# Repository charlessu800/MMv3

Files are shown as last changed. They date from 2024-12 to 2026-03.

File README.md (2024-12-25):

# MMv3

MMv3 is the 3rd generation robot platform used to teach the IEEE Micromouse DeCal at UC Berkeley. It was designed with usability, manufacturability, size, and cost in mind.

## Schedule

Skeleton lab code, lab documents, and solutions are stored in [labs/](labs/), [docs/](docs/), and [solutions/](solutions/), respectively. To get started with a lab, simply copy the contents of the folder over to the CircuitPython drive and edit files from there.

* [lab1](docs/lab1.md) - CircuitPython Basics
* [lab2](docs/lab2.md) - Assembly
* [sanity](docs/sanity.md) - Hardware Check
* [lab3](docs/lab3.md) - Encoders
* [lab4](docs/lab4.md) - IR Sensors
* [lab5](docs/lab5.md) - Odometry and Motor Control
* **Checkpoint 1**: Does your mouse drive?
* [lab6](docs/lab6.md) - Intro to PID
* [lab7](docs/lab7.md) - More PID
* **Checkpoint 2**: Does your mouse straight under PID control?
* [lab8](docs/lab8.md) - Maze Solving Primitives **(WIP)**

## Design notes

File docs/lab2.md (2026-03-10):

# Lab 2: Assembly

## Quick Check

First thing you should do before you move on with the rest of the lab is to plug your Pi Pico into your computer and make sure it shows up in your file system like so: 

(NOTE: the image below shows a drive named CIRCUITPY but you probably will see a drive named RPI-RP2. This is expected)
<p align="center">
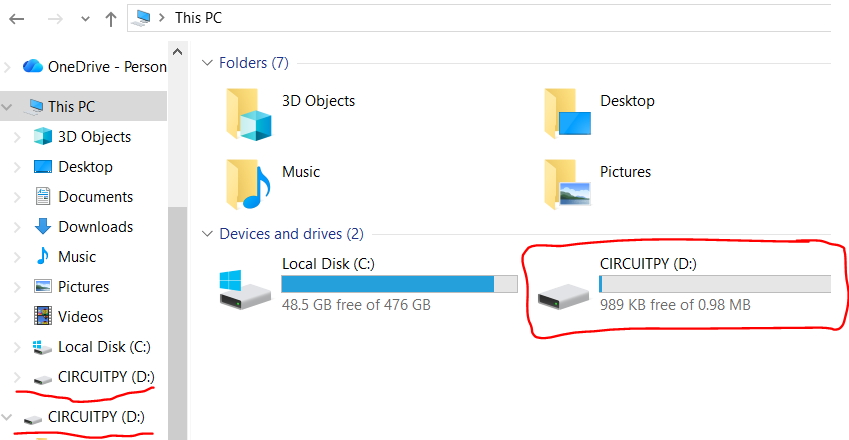
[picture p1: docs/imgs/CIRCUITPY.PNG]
    
    <br>
    <a><b>Updated CIRCUITPY Drive Directory Example image in Windows 10 File Explorer</b></a>
</p>
If the Pi Pico when connected to your PC does not show up like the image above shows try a different cable. If that does not work, try a different PC. Finally, if all the above does not work ask your TA for help.

## Assembly

Download [`ibom.html`](https://github.com/charlessu800/MMv3/releases/download/MMv3.5/ibom.html) and open it in your preferred browser. The interactive BOM (bill of materials) shows what parts are needed on your mouse's PCB (printed circuit board) and where they need to be placed. This html file will be very helpful when assembling your mouse.

To see images of all the individual parts, see the Google Drive link [here](https://drive.google.com/drive/folders/1rGae82BSrE_mvmMwKTBHT9P-unDKIKQj?usp=sharing).

### Reflow Soldering

Let's start with the back of the PCB which is where the majority of parts are located. In the `ibom.html` file you have downloaded then opened in your a browser, click `B` in the top right (highlighted in red) to show just the back side of the PCB. Make sure it looks like below.

<p align="center">
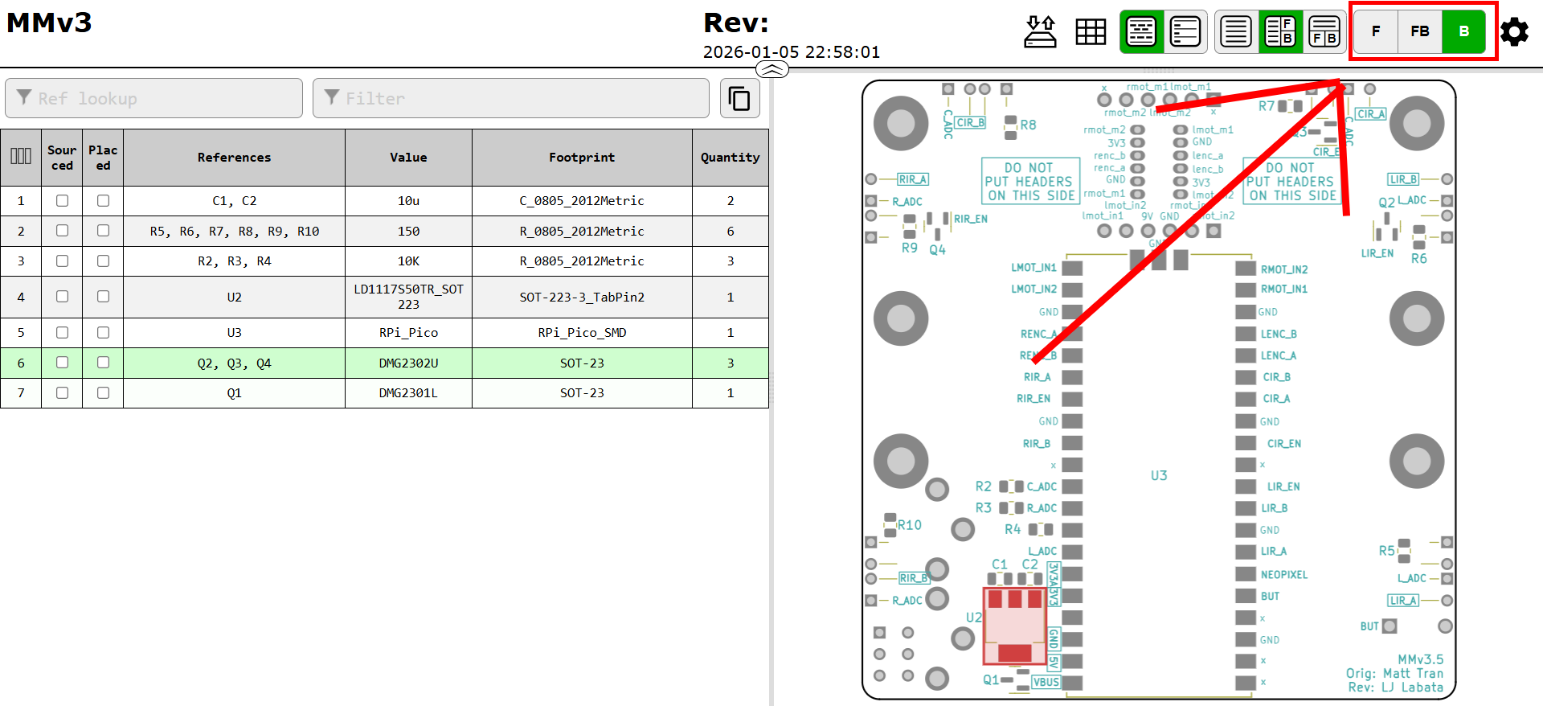
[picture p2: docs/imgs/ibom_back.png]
    
    <br>
    <a><b>iBOM Back</b></a>
</p>

Rather than solder each part by hand, we'll use reflow soldering which does it all at once. In reflow soldering, we place components on top of pads covered in solder paste before sending the whole thing through an oven to melt the solder, making permanent joints.

<p align="center">
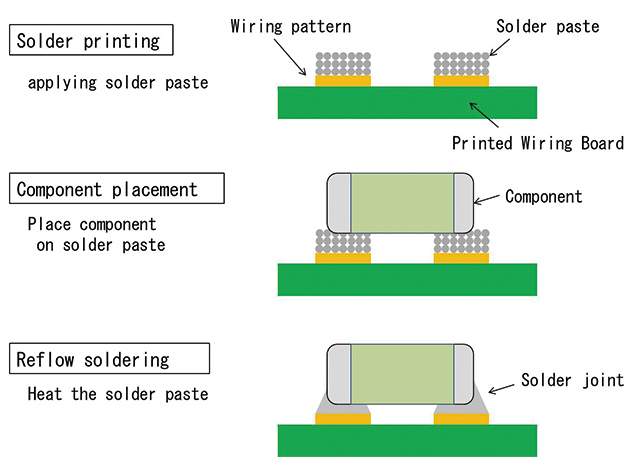
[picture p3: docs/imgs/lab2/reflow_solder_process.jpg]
    
    <br>
    <a><b>Reflow Solder Process</b></a>
</p>

Let's start by applying the solder paste using a **solder stencil**. Instead of squeezing the perfect amount onto each pad by hand, we can do it all at once by spreading paste over a stencil with holes cut out precisely where we want paste. For a good solder paste application, it's important to make sure the stencil is flush against the PCB and stays aligned. Tape the stencil onto the table to keep the stencil from moving. The process is very forgiving, so don't worry if your paste looks messy or goes a bit outside the pads after having applied the paste with the stencil. You can use tweezers or something like it to clean up places where pads are shorted togehter. Please ask the TAs if you have any questions about this.  

<p align="center">
    
    
    
    <br>
    <a><b>Solder Paste Application Process</b></a>
</p>

Now it's time for component placement. Following the `ibom.html`, place all of the components for the back side. None of the symmetric components have polarity, so don't worry about part orientation. Tweezers will be very useful, but don't squeeze too hard or your component will go flying. Again, the process is quite forgiving so don't worry if your parts aren't perfectly aligned as solder surface tension will generally pull them into alignment.

<p align="center">
    
    
    
    <br>
    <a><b>Component Placement</b></a>
</p>

> [!IMPORTANT]  
> Before moving on, double check that you correctly placed each component in the right place and the right orientation.
> - Are your MOSFET transistors in the right place? Remember that there are 3 x n-channel MOSFETs (Q2,Q3,Q4) and **1 x p-channel MOSFET (Q1)**.
> Now you are ready to show one of your TAs to give it one last lookover before getting reflowed.

Finally, let's reflow the solder! Bring you board with the placed components to your TA. They will do a final check before throwing your board into the reflow oven, loading up the correct profile, and waiting. With any luck, all of your joints will melt and the back side of your board will be done.

<p align="center">
    
    
    <br>
    <a><b>Reflow</b></a>
</p>

### Hand Soldering

The rest of the components need to be attached by hand. The general process is to heat up both the pad and the part before melting solder onto both of them. Adafruit has a great list of common issues and fixes which can be found [here](https://learn.adafruit.com/adafruit-guide-excellent-soldering/common-problems).  

<p align="center">
    
    <br>
    <a><b>How to Make a Solder Joint</b></a>
</p>

Let's start off with the mouse's main PCB. Click `F`, located in the top right of the `ibom.html`, to see the remaining components.

<p align="center">
    
    <br>
    <a><b>iBOM Front</b></a>
</p>

You can hand solder all the components on the Front side of the PCB in any order but there is a preferred way to do so that will be less of a headache when soldering.
1. D2 - D13 (THT LEDs)
2. SW1, SW2 (THT Switches)
3. DRV8833 (Motor Drive Module)
4. J3, J4 (ZH Series JST 6-pin connector)
5. J2, J5 (Receptacle Connector 0.100" (2.54mm) Through Hole Gold)
6. J1 (Keystone_593_594 Battery Contact Snaps)

This is also the order in how the lab has been laid out.

First we solder the IR LEDs. Note that the silkscreen should denote the polarity. The longer line corresponds to the longer leg of the IR LEDs. They also need to be mounted at a right angle so don't be afraid to bend them. Splaying the leads outward should hold them in place while you apply solder. After you solder them you can cut off the excess legs of the IR LEDs but be careful! The ends will fly off when cutting so protect your eyes. Look away if you don't have glasses ;(

<p align="center">
    
    
    <br>
    <a><b>IR LEDs</b></a>
</p>

Next, solder the SW1, SW2 (THT Switches). These components do now have polarity so their orientation does not matter. Additionally, you should solder these switches such that they are on the Front side of the board but if you do not that is okay. They still will work.
<p align="center">
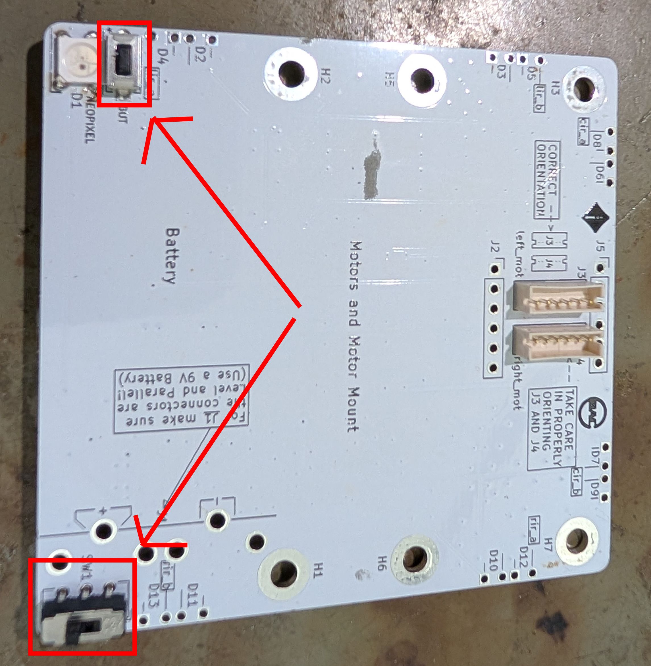
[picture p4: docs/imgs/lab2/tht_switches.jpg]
    
    <br>
    <a><b>THT Switches</b></a>
</p>

Now, the DRV8833 motor driver board. Solder the two 6-pin headers onto the board and bridge the `en` pads as shown in the following pictures. Make sure when soldering the two 6-pin headers that you are placing them on the correct side of the board. It should look like the final image below where the `en` pads are on top.

The technique that I find works best is to solder just one pin first with the part in any orientation. Then reheat that joint while pressing on the part to move it into perfect alignment. Finally, do the rest of the pins.

<p align="center">
    
    
    
    
    <br>
    <a><b>DRV8833 Motor Driver Assembly</b></a>
</p>

Finally, let's add the connector components! We saved these for last because if we did them any sooner it would make soldering the rest of the board more awkward. This is because the bigger components, like the battery connectors and motor connectors, would make it almost impossible to lay the pcb flat on a table.

> [!NOTE]
> Be sure that when you solder these bigger components, motor connectors and such, you place them on the correct side of the board, the Front side. That side is the side opposite of the pi pico. DO NOT solder these bigger components on the same side as the green pi pico. You will save yourself a lot of headaches :D

Lets start by soldering first the J3, J4 (ZH Series JST 6-pin connector) components

<p align="center">
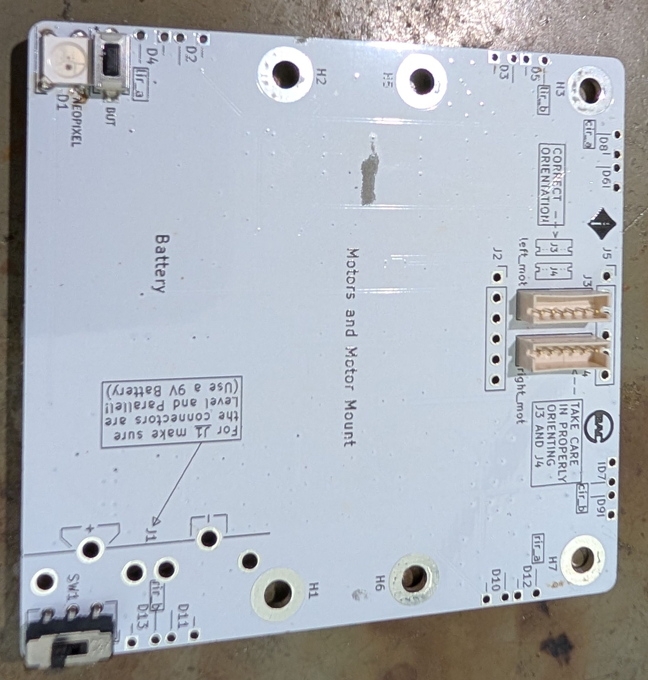
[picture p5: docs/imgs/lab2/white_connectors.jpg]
    
    <br>
    <a><b>J3, J4 (ZH Series JST 6-pin connector)</b></a>
</p>

Next solder first the J2, J5 (Receptacle Connector 0.100" (2.54mm) Through Hole Gold)

<p align="center">
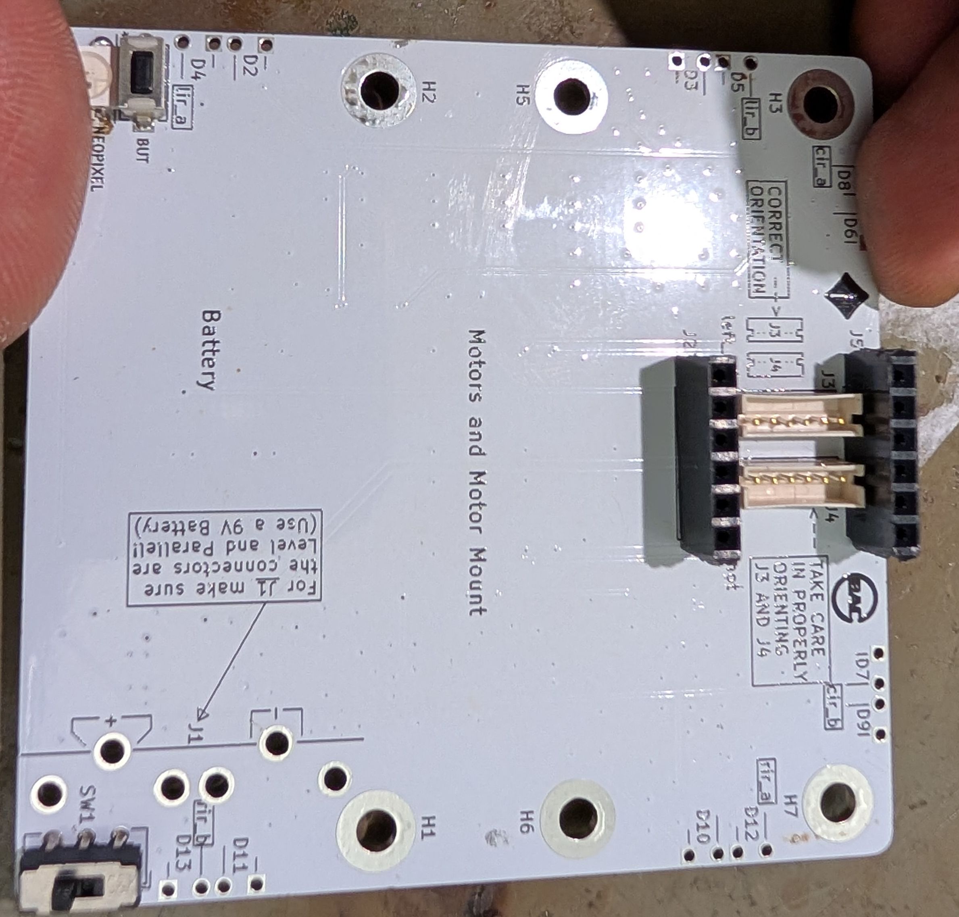
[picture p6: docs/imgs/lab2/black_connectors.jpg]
    
    <br>
    <a><b>J2, J5 (Receptacle Connector 0.100" (2.54mm) Through Hole Gold)
</b></a>
</p>

Now let's solder the J1 (Keystone_593_594 Battery Contact Snaps) connectors. When soldering these connectors it is advised to take the two Battery Contact Snaps, positive and negative, and attach them to a 9V battery first before placing them on the board. See the images below. This is to make sure that when you solder them onto the board they are aligned. You can solder the Battery Contact Snaps while the 9V battery is still connected to them. (In these photos the directionality of the motor contorller unit is facing the wrong way, the point where you bridge the pads should be closer to the left side.) 

<p align="center">
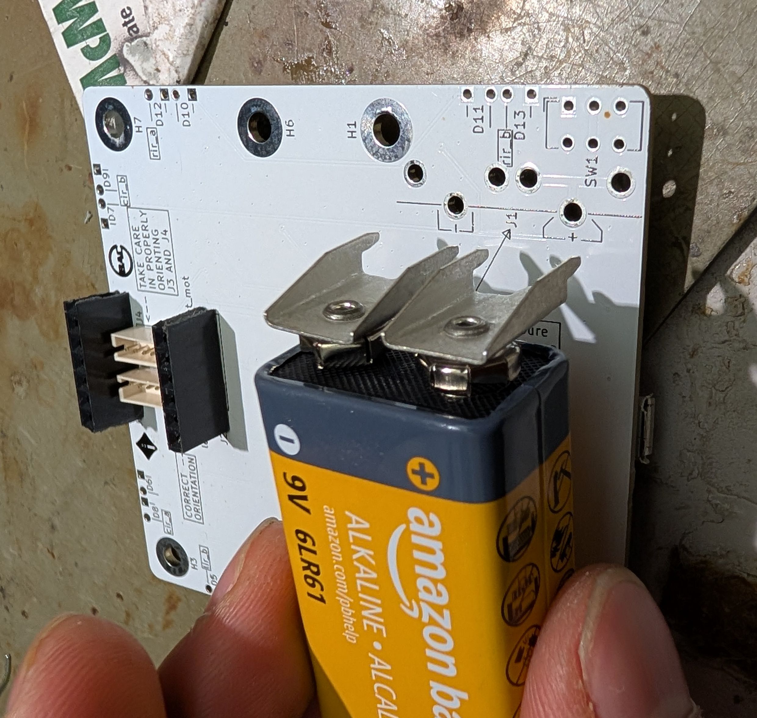
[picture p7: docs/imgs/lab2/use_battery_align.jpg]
    
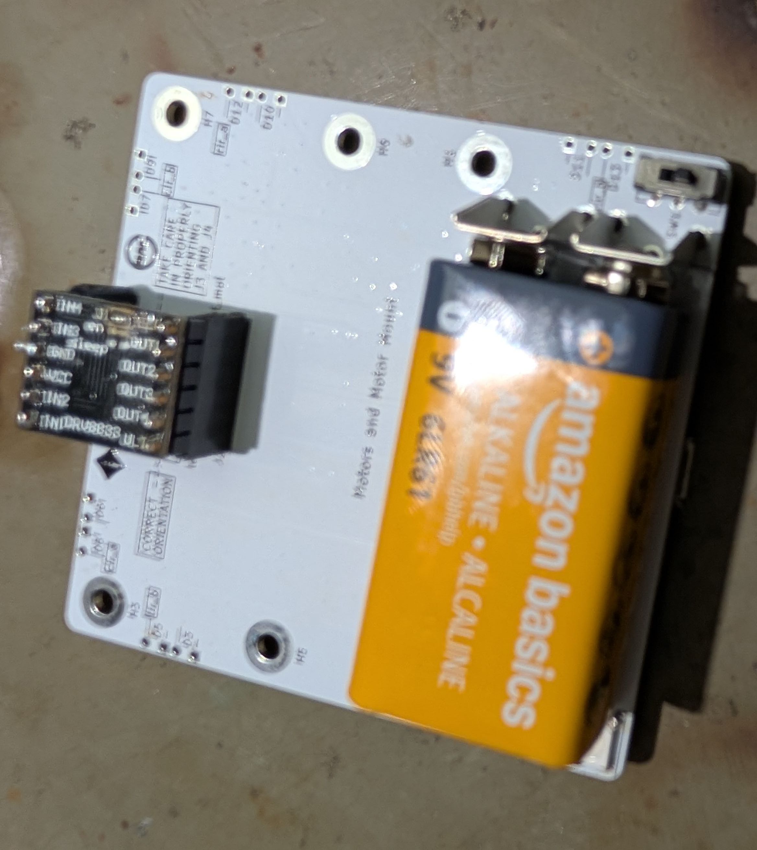
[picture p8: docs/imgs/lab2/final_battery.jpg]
    
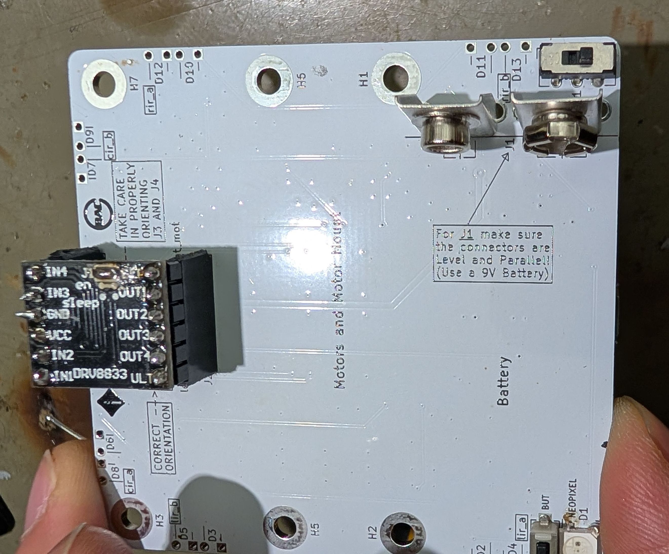
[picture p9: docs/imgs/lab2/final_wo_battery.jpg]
    
    <br>
    <a><b>Using a 9V Battery for Alignment of the J1 (Keystone_593_594 Battery Contact Snaps)
</b></a>
</p>

Additionally, make sure that you place the two Battery Contact Snaps in each of their respectative places. 

<p align="center">
    
    <br>
    <a><b>Good Placement
</b></a>
</p>

<p align="center">
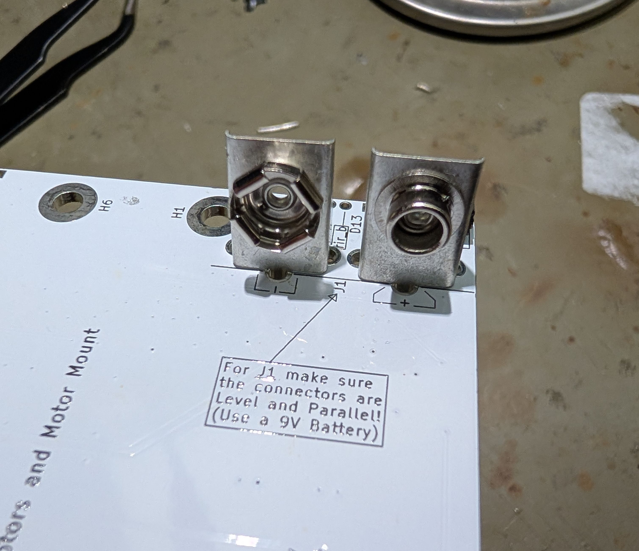
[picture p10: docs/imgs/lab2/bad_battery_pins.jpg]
    
    <br>
    <a><b>Bad Placement
</b></a>
</p>

With any luck, your board should be finished! At least all the soldering :)

<p align="center">
    
    <br>
    <a><b>PCB with completed soldered components</b></a>
</p>

### Optional SMD LED Component

We made the D1 Neopixel LED component optional as it's one of the hardest parts to solder. It is the only hand soldered SMD component. The Neopixel LED uses the same soldering process except there's no hole to stick the part through. Please see this [video (skip to 2:16)](https://youtu.be/RODp8HSlFPA?t=136) on soldering such components if you want to give this a try. You will need tweezers.

<p align="center">
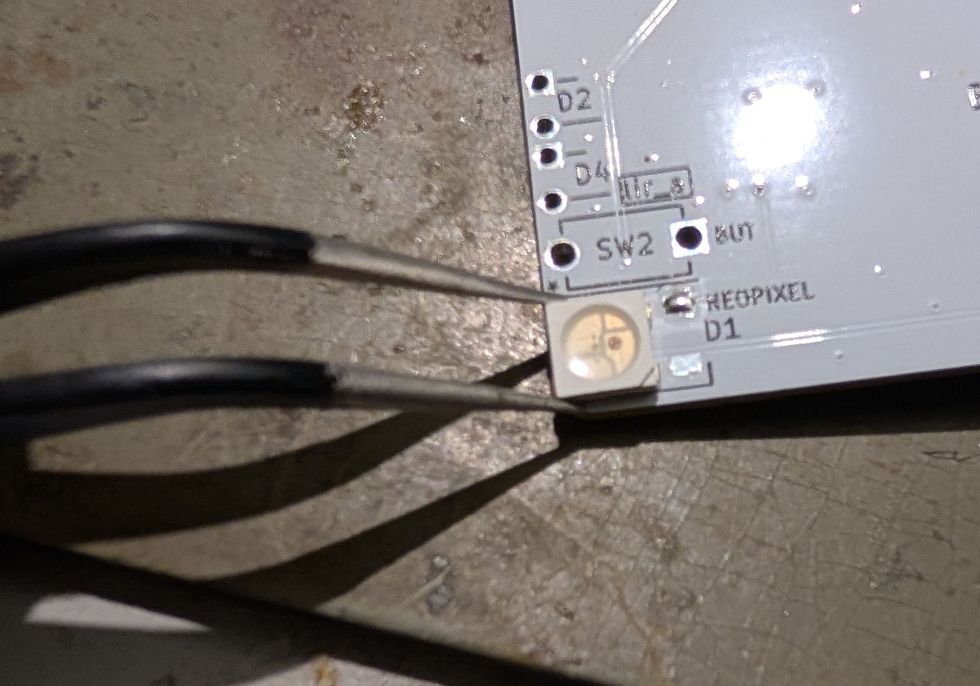
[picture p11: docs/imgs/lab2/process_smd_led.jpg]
    
    <br>
    <a><b>Part of the process to solder D1 Neopixel LED with tweezers</b></a>
</p>

> [!NOTE]  
> The Neopixel has a polarity or in other words a specific orientation that it must be placed in when soldering. You must place this part correctly in order for this Neopixel LED to work. Align this triangular indent on the Neopixel as shown below when soldering, highlighted in red. 

<p align="center">
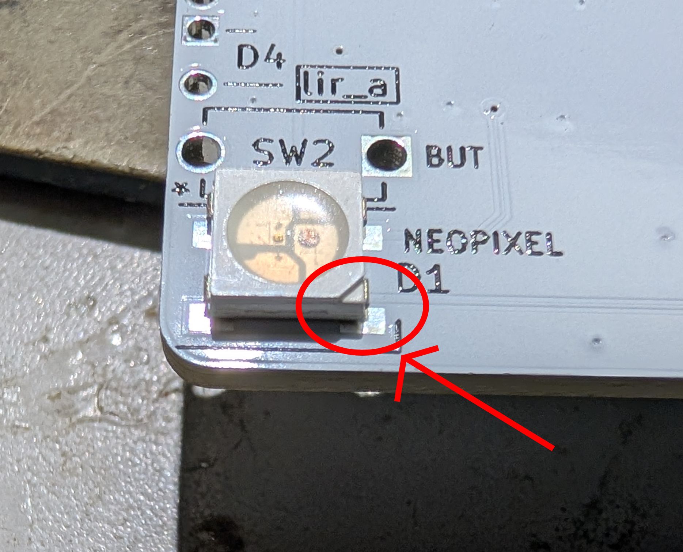
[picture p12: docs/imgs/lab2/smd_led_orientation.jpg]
    
    <br>
    <a><b>SMD LED Proper Orientation</b></a>
</p>

### Partial Mechanical Assembly

We will only partially assembly the mechanical parts of the mouse first before assembling it all in one go. We do this to make swapping out motors easier if one motor does not work (hopefully not the case). So just connect the put the motors into their 3D printed motor housing and connect them to the board using the cables for now. Then check if the motors work by running the sanity check that we talk more about below.

<p align="center">
    
    
    <br>
    <a><b>Partial Assembly</b></a>
</p>

> [!IMPORTANT]  
> Make sure that when you plug in the motor cables that they are plugged in all the way. Below are what a good motor cable plugged connection looks like and a bad one. Do this before running the sanity check code.

<p align="center">
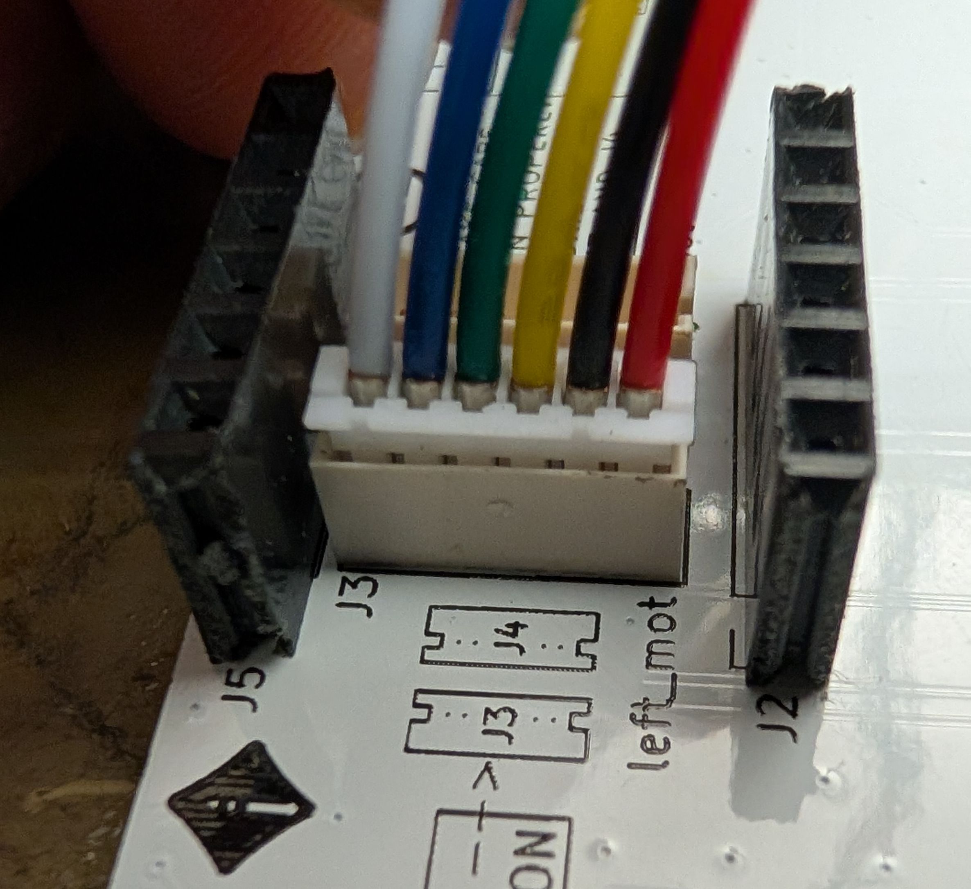
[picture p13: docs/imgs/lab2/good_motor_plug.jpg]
    
    <br>
    <a><b>Good - Motor Cables plugged in all the way</b></a>
</p>

<p align="center">
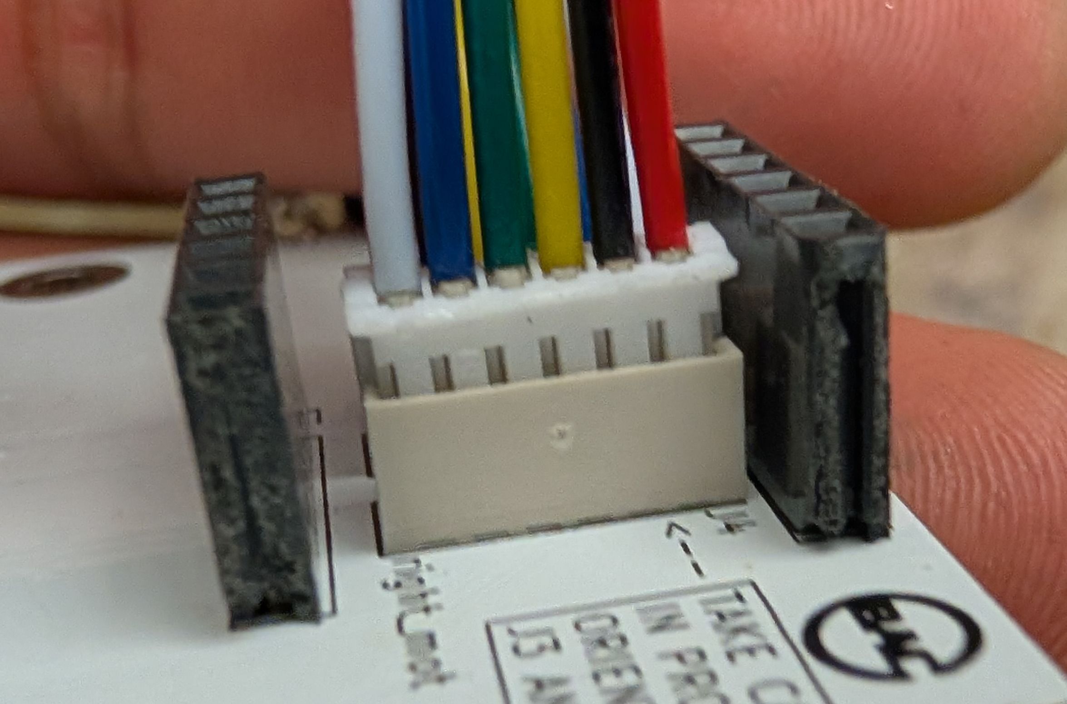
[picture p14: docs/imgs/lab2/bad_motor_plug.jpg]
    
    <br>
    <a><b>Bad - Motor Cables not plugged in all the way</b></a>
</p>

## Sanity Check

Now before we fully assembly your mouse we will make sure everything is working by running a [sanity check](sanity.md).
That means check to see that each of the 6 pairs of IR LEDs work, that each of the two motors spin as they should, and that the encoders work by outputting data that makes sense. You can find out more of what this means by following the [sanity check](sanity.md) document. 

## IR Calibration

If you placed your mouse against a reflective surface, you may have noticed that the IR readings change. Since our sensors are currently mounted perpendicular to the mouse, they pick up some reflection from the surface the mouse sits on. To fix this, we're going to bend our IR sensors ever so slightly upwards to compensate.

Bring up the sanity check again to the IR sensor printout section. Bend your IR sensors upwards just enough so that the difference between pointing them into free space and placing them on a surface is less than 2,000.

<p align="center">
    
    <br>
    <a><b>Bent IR Sensors</b></a>
</p>

### Final Mechanical Assembly

Yay you made it! Let's finish assembling the mouse. Follow the pictures below. The screw threads are printed into the plastic so don't overtighten them. Don't be afraid to apply a bit of force when attaching the wheels since a tighter fit improves concentricity.

<p align="center">
    
    
    
    
    
    <br>
    <a><b>Final Assembly</b></a>
</p>

### Checkoff #1

1. Show your mentor your assembled mouse, passing sanity check, and calibrated IR sensors.

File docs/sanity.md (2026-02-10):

# Sanity

This lab provides the instructions and code to test all aspects of your mouse and identify any hardware defects. If at any point in this lab a test is not passed, refer to this document to [troubleshoot](troubleshooting.md) your mouse. If, after trying to troubleshoot your mouse on your own with the aforementioned document, it is still not working, ask an instructor for further help debugging.

1. Upload the firmware onto your Raspberry Pi Pico

Plug the mouse, aka the Pi Pico, into your computer and upload the latest **firmware.uf2** (see [releases](https://adafruit-circuit-python.s3.amazonaws.com/bin/raspberry_pi_pico/en_US/adafruit-circuitpython-raspberry_pi_pico-en_US-8.2.0.uf2) by dragging the file into the `RPI-RP2` folder that shows up. The RPI-RP2 folder is shown in the following image.

[TODO: ADD RPI-RP2 Drive Directory Example image]
*RPI-RP2 Drive Directory Example image*

It should disappear and reappear as a `CIRCUITPY` folder. As the following image shows.
<p align="center">
    
    <br>
    <a><b>Updated CIRCUITPY Drive Directory Example image in Windows 10 File Explorer</b></a>
</p>

> [!NOTE]  
> If you've uploaded firmware before onto the Pi Pico, you'll need to hold the `BOOTSEL` button on the Pi Pico while plugging in. In more detail, first make sure to unplug the Pi Pico from your computer, then hold the `BOOTSEL` button on the Pi Pico. Then, while holding the `BOOTSEL` button, plug the Pi Pico back in. The Pico should appear as a  USB Mass Storage Device, RPI-RP2. You can now stop holding the `BOOTSEL` button. (For more information, see: [Chapter 4. Applications information
4.1. Programming the flash](https://pip-assets.raspberrypi.com/categories/610-raspberry-pi-pico/documents/RP-008307-DS-1-pico-datasheet.pdf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))

2. Upload the CircuitPython libraries and custom firmware onto your Pi Pico

Download this [sanity.zip](https://github.com/charlessu800/MMv3/releases/download/MMv3.5/sanity.zip) file and unzip it into your Pi Pico directory. Your Pi Pico's directory should now look like this, with all the newly added files and folders:
* CIRCUITPYTHON/
    * **lib/**
        * **adafruit_motor/**
        * **adafruit_onewire/**
        * **neopixel.mpy**
    * **ds28e05.py**
    * **irsensor.py**
    * code.py

(**Bolded text represents the new files and folders that you will have added**)

If the .zip file method above is not working, then you can follow the steps below to manually download the files from CircuitPython and GitHub.
<details>
<summary>Alternatively, Manually Download From CircuitPython and GitHub</summary>

Download the CircuitPython [libraries](https://circuitpython.org/libraries) (Bundle for Version 8.x or 7.x, 9.x is untested! If you'd like you could test it for us ;) ), right click on 8.x -> open in new tab, unzip the file and upload the following folders and files to the lib/ folder on your mouse.
* adafruit_motor/
* adafruit_onewire/
* neopixel.mpy

Upload these files from this folder, [labs/sanity](../labs/sanity), into the top level of the Pi Pico directory.
* ds28e05.py
* irsensor.py
</details>
<br>

3. Upload the Sanity program code into your Pi Pico

Copy the contents of this [`sanity/code.py`](../labs/sanity/code.py) file into your Pi Pico's already existing `code.py` file. You will need a text editor to open up this file (shown in the image below) to copy and paste the sanity code. I would recommend you use VSCode, but any text editor can do. If you do not know how, please ask one of our TAs for help :)

<p align="center">
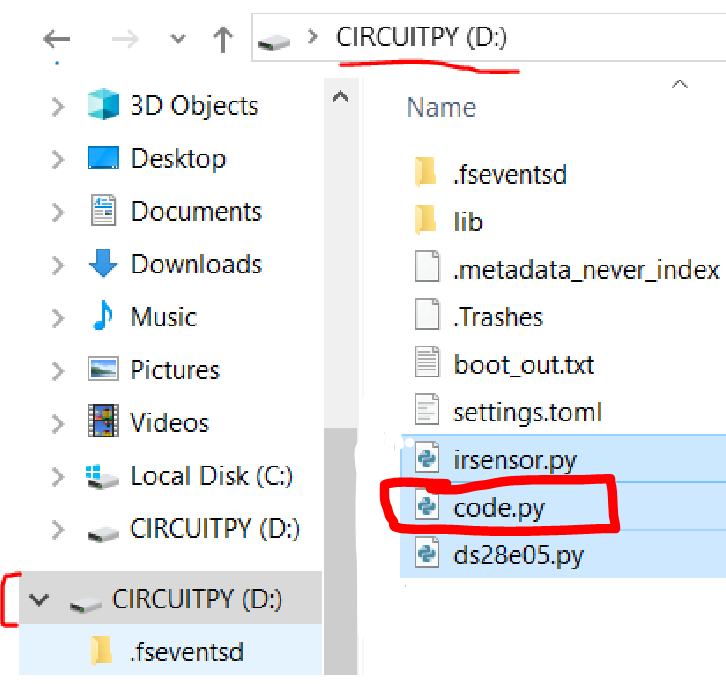
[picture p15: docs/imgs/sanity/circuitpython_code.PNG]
    
    <br>
    <a><b>Location in your Raspberry Pi Pico of where to paste the files into</b></a>
</p>

4. Find the associated serial port for your mouse.
    <details>
    <summary>Windows</summary>

    Open up `Device Manager` and check the `Ports (COM & LPT)` dropdown. Your serial (COM) port is one of those. If it's hard to identify, try unplugging and replugging your mouse and see which COM port disappears.

    </details>
    <details>
    <summary>MacOS</summary>

    Run `ls  /dev/tty.*` in Terminal. The correct port is one of those. If it's hard to identify, try unplugging and replugging your mouse and see which port disappears. It should be something like /dev/tty.usbmodem101

    </details>
    <details>
    <summary>Linux</summary>

    Hello there! A fellow power user you are. Your distro may be different, but chances are it's under something like `/dev/ttyACM0`.
    </details>

5. Bring up a serial monitor on that serial port (baud rate doesn't matter). There are many options of software to use, but the following are what I personally use.
    * **Windows** - [PuTTY](https://www.chiark.greenend.org.uk/~sgtatham/putty/latest.html) Open up putty -> Serial -> Enter COM[X] -> Run
    * **MacOS** - [SerialTools](https://apps.apple.com/us/app/serialtools/id611021963?mt=12) or [screen](https://en.wikipedia.org/wiki/GNU_Screen) after running ls /dev/tty.* youre going to type into your terminal -> screen "whatever you identified as the correct port". Then press control-c or control-d, you should see some text pop up! If this doesn't work, its a bit finiky, open up serialTools to the terminal tab change your serial port to the usb you identified and press the connect button on the right hand side. After, press control-c or control-d. If this doesn't work try going back to screen or using the VScode Serial tools extensions
    * **Linux** - [screen](https://en.wikipedia.org/wiki/GNU_Screen)
6. Follow the instructions printed in the serial monitor. You may have to press CTRL-C and CTRL-D to reset if you don't see anything.
    * IR sensor readings should be around 30,000-60,000 without a surface in front of them and under 5,000 with your hand right in front of them. Speak to a staff member if you need help with this part of the lab!
    * Spin the wheels manually, Encoders should be \~217 ticks per revolution, use the divot in the wheel as a guide :).
### Using the VSCode serial tools Extension
In VSCode navigate to your extensions, download the serial monitor extension
1. Navigate to the extension  
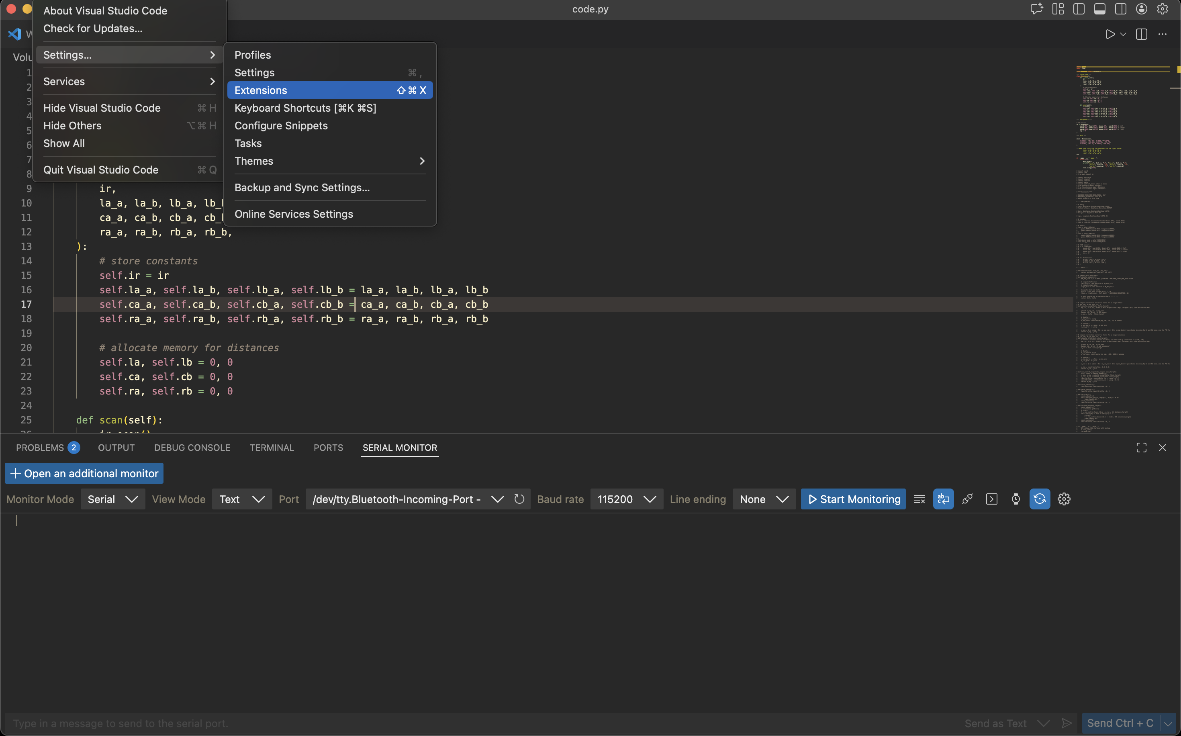
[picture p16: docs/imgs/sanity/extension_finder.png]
   

3. Download the extension finder  
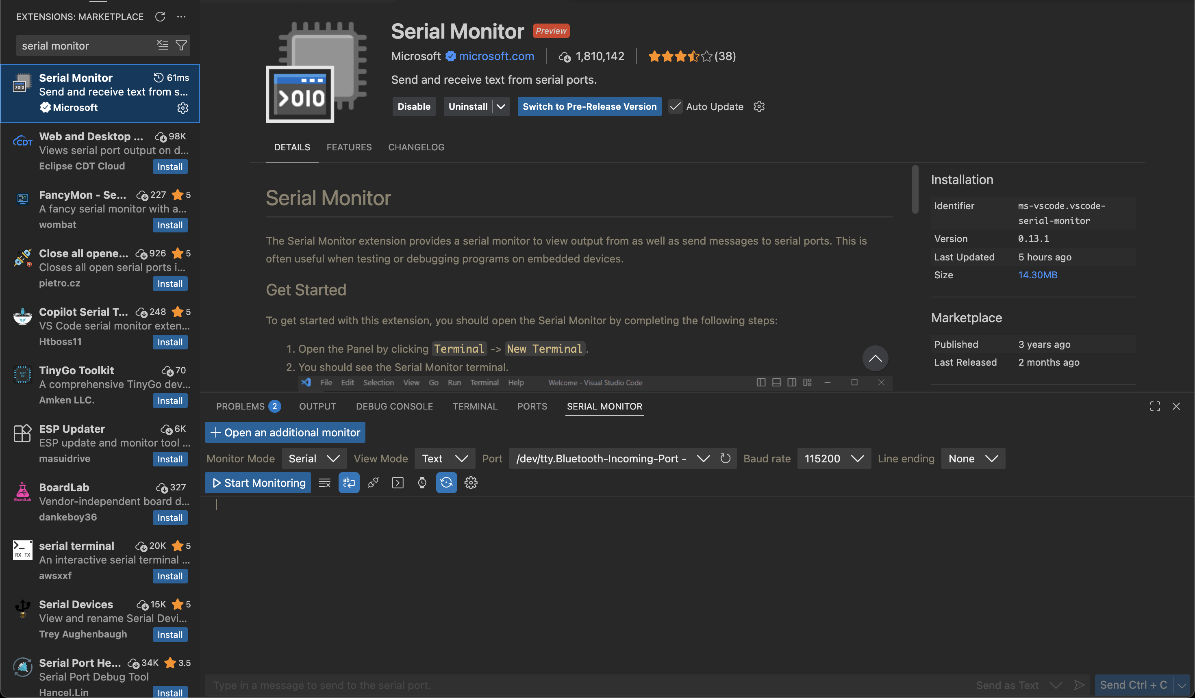
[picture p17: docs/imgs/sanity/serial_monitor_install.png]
   

5. Stop / Start monitoring  
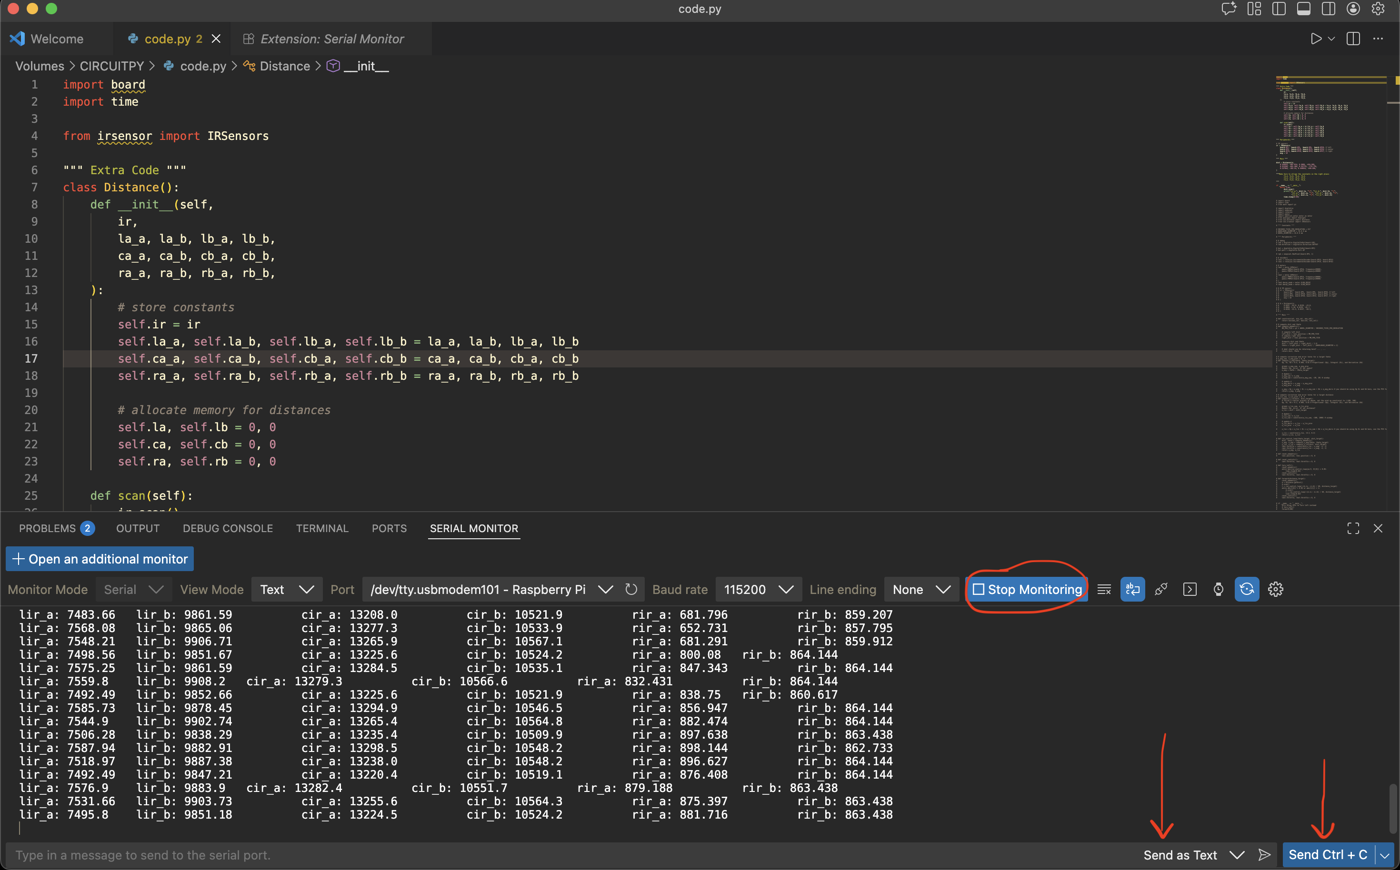
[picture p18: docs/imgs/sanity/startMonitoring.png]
   

Use CTRL-c to manually interupt the program, or CTRL-D to specify no more input 

[TODO: update the following below to include circuitpython . org and vscode with serial monitor extension! For both mac/linux/windows etc! and also include the mu text editor. Also add more photos!]

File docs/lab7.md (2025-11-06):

# Lab 7: More PID

## Background

In the previous lab we were able to get our mice driving a certain distance reasonably straight with just proportional control. This week, we'll learn how to correct for persistent steady state error, turn in place, and follow walls.

Recall our implementation of a **proportional (P) controller** from the last lab.

<p align="center">
    $u(t) = K_pe(t)$
</p>

Proportional control works pretty well for making our mouse drive straight, but you may have noticed a constant offset error. The motors naturally travel at different speeds given the same power and the constant offset error actually accounts for that difference. If we had zero error, we'd actually apply the same power to each motor, generating an error. How might we fix this? What if we kept track of the total error?

<p align="center">
    $u(t) = K_pe(t) + K_i\int_0^t e(\tau) d\tau$
</p>

This is called a **proportional-integral (PI) controller**. The integral keeps track of the total error (both positive and negative) since we first started the controller. Even small errors will cause the integral term to eventually grow large enough and get $u(t)$ to push our mouse back on track.

In order to dampen oscillations and prevent overshoot, we might want to consider the derivative of our error too. This prevents our error from changing too quickly.

<p align="center">
    $u(t) = K_pe(t) + K_i\int_0^t e(\tau) d\tau + K_d\frac{de(t)}{dt}$
</p>

With these three terms, we have our **proportional-integral-derivative (PID) controller**. $K_p$, $K_i$, and $K_d$ are tunable gains that determine the behavior of our error (rise time, peak, overshoot, etc.).

Let's go over what each of the terms in PID means.

* The **P** term (**proportional**) increases our correction proportionally to the error: the higher our error, the more power we should apply to correct for it.
* The **I** term (**integral**) compensates for long-term error and drift by integrating the error over time. While a small tendency for our mouse to veer to the right might have little effect on the P term, it’ll cause the I term to build up until the system reaches the setpoint perfectly.
* The **D** term (**derivative**) takes the derivative of the error with respect to time. Systems often have inertia: the faster our error is already decreasing, the less power we need to apply to correct for it. This dampens our controller and reduces overshooting.

Note this checkpoint has no code.

### Checkoff #1

1. We only have individual measurements of error, not a continuous function. How might we estimate the integral of the error?
2. How might we estimate the derivative of the error?
3. One potential issue with PID control is **integral windup**. You can read about it [here](https://en.wikipedia.org/wiki/Integral_windup). What are some ways of preventing integral windup?

## Turning

Copy over the skeleton code in [labs/lab6/](../labs/lab6) onto your mouse. To encourage code readability, we've added a couple of function definitions that modularize the controller. Adapt your P controller code from [Lab 6](lab6.md) to these functions by filling out the TODOs. If you have a better way of organizing the functions, feel free to change things. Ultimately, it should have the same behavior as Checkoff #2 from Lab 5.

Next, add I and D terms to both your angular and linear P controllers. You may find the `global` or `nonlocal` keywords to be useful for accessing variables defined outside of a function. We highly recommend just tuning the PID constants for your linear controller first and then tuning the angular controller when you implement turning. It's generally easier when that specific controller is being exercised. Good starting values are 10x smaller than $K_p$.

Finally, have your mouse turn 90° in place. This should be as simple as setting a different target $\theta$. For an added challenge, let's create a `turn_left` function which internally loops until the mouse turns about 90° (you choose the threshold for acceptable error) before returning. You may find it useful to be able to reset the odometry back to 0 with the following function.

```python
def reset_odometry():
    lenc.position, renc.position = 0, 0
```

### Checkoff #2

1. Demonstrate your working PID loop driving straight a set distance.
2. Demonstrate your working PID loop turning in place by 90°.
3. Demonstrate turning in place by 90° and then stopping for one second before turning another 90° and so on.
4. Explain your implementation of your integral term. Did you account for integral windup?

## Wall Following

When we're driving in a maze, our mouse will always be slightly misaligned with reference to a wall. Despite driving perfectly straight, this slight error will eventually cause us to crash. By performing feedback control with our IR sensors, we can correct for any misalignment!

In the interest of developing maze solving primitives in the future, you will implement a `forward()` function that will have the mouse drive forwards 180mm (~7in) and stop. While driving forward, maintain a fixed 45mm distance from a wall on the left.

Optimally, stable wall following means maintaining a 0° angle with respect to the wall. With just one sensor, it's impossible to determine the angle because multiple angles can correspond to the same sensed distance. Performing feedback control on just that sensor works, but it relies on the mouse moving a bit to correct for angular errors. With two sensors, we can determine the angle from the wall based on the difference between the sensors. Wall following could then be implemented as just setting the angle of the mouse based on the distance error and letting its forward motion correct for the distance error.

To implement wall following, start by taking your distance measurement code from lab 3 and your linear and angular PID controllers from the previous checkoff. Conceptually, we want to change the definitions of `theta` and `theta_target` for the angular controller. Based on what was discussed previously, what are the new definitions of `theta` and `theta_target`?

Don't worry about implementing a PID controller for this as a P controller is adequate. Tuning can be a bit tricky. We've found that `Kp_theta=0.01` and `Kp_ang=0.01` work pretty well. Our reference solution uses `Kp_theta` to scale the distance error to set `theta_target`. Since we assume the mouse drives pretty straight and isn't very misaligned, don't worry about tuning your controller to work well for large errors.

### Checkoff #3

1. Demonstrate your wall following code by calling `forward()` once every second.
2. How might you extend your code to drive straight in between two walls?

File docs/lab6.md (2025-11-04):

# Lab 6: Intro to (P) of PID

## Background

You'll need your code from lab five here!!
You may have noticed that if you let your mouse drive forward for long enough, it'll start drifting to one side. That's because we're just using open-loop control where we apply some input and hope we get the desired output. For various reasons, including but not limited to the following, our mouse will not drive straight even given the same power to both motors.

* The mouse isn't perfectly balanced as all things should be.
* The ground is not perfectly flat.
* Our motors aren't exactly the same.

To fix this, we'll apply something called closed-loop control. Also known as feedback control, we take measurements from the encoders to adjust the power to our motors and drive straight. For example, if we are veering to the left based on encoder readings, we can increase power to the left motor and decrease power to the right motor to correct it.

One common way to do feedback control is PID. For now, you'll be implementing just the P part of it. Conceptually, feedback controllers try to minimize some error which is the difference between a measured value (aka process variable) and setpoint.

For a P controller, we vary our motor power proportionally to our error. That is, the larger our error, the more power we apply to correct for it.

<p align="center">
    $u(t) = K_pe(t)$
</p>

## Drive Straight

Copy over the skeleton code in [labs/lab5/](../labs/lab5) onto your mouse. Our code is getting too long to just copy paste every time. By default, the code makes the mouse drive forward at 20% speed. Next, copy over your code from [Lab 5](lab5.md) to compute `dist` and `theta` based on encoder readings.

Your job is to apply P control to make the mouse drive straight. The linear velocity doesn't matter too much, just the fact that it doesn't veer left or right. To do this, it would help to answer the following questions.

* What is $\theta$ when driving straight?
* What is the error when driving straight?
* Given an error, how do you change each motor's power to correct for it?

When implementing the P controller, start with $K_p$ values of around 0.1 and tune up and down from there based on performance. To make sure the mouse does move forward, add 0.2 to the `throttle` for each motor in addition to your correction term.

$K_p$: proportional gain. This value is responsible for determining how strongly we'll be correcting for error. 

``` python
... 
# import statements
# Define these 
# Constants 
# Encoders
# Motors
...
lmot.decay_mode = motor.SLOW_DECAY
rmot.decay_mode = motor.SLOW_DECAY

def constrain(val):
    return min(1, max(val, -1))
if __name__ == "__main__":
    MM_PER_TICK = ...

    while True:
        # Calculate the left distance value
        left_dist = ...
        # Calculate the right distance value
        right_dist = ...
        # Get both theta and distance from lab 
        dist = ...
        theta = ...

        # set Kp to a low value to begin, 0.1 etc, what do you notice when you vary this? 
        k_p = ...
        # What is our target theta value?
        theta_target = ...
        # whats the error of our target and the theta?
        angular_error = ...
        
        # define the steering correction, Our correction should be proporitonal to our angular error
        # the action
        steer_correction = ...
    
        #set the throttles of the left/right motor.
        # Lets constrain it to 0.2 plus or minus our steering correction depending on the motor
        lmot.throttle = constrain(...)
        rmot.throttle = constrain(...)

        print(angular_error)
    
        time.sleep(0.05)
```

After implementing this code, place your mouse on the ground and let it go straight. You likely won't get a perfectly straight mouse, this code by itself is not enough to completely correct our motor's direction; though it should be slightly better than just forward. This is fine for shorter distances purpose, but you'll quickly see your mouse veer off when it travels further than a few inches.

### Checkoff #1

1. Demonstrate your working P controller. Print out your error term too.
2. How do you compute the error term?
3. If we want our applied correction power $u(t)$ to be maximized $(u(t) = 1)$ when the error is 2 radians, what is $K_p$?
4. What happens when $K_p$ is too low? How about too high? What value did you end up using?

## Go the Distance

When solving mazes, it is quite useful to be able to drive forward a set distance. Let's swap out the 0.2 we blindly added to the `throttle` for a linear correction term. Your job is to get your mouse to drive straight forward 200mm (~8inches) and then stop. Like with driving straight, it'd help to answer the following questions.

* What is the error for traveling a set distance?
* Given an error, how do you change each motor's power to correct for it?

When implementing the P controller, start with $K_p$ values of 0.1 and tune. Don't remove your angular correction code from before since we still want to drive straight. Since we want to leave a little wiggle room for the angular correction, limit the linear correction term to around 0.3.

```python
...
def constrain(val, min_val, max_val):
    return min(max_val, max(val, min_val))

if __name__ == "__main__":
    MM_PER_TICK = ...

    while True:
        left_dist  = ...
        right_dist = ...

        dist  = ...
        theta = ...

        # angular P control
        k_p = ...
        theta_target = ...

        angular_error = ...
        steer_correction = ...

        # linear P control
        Kp_lin = ...
        dist_target = ... # in mm

        # linear error?
        lin_error = ...
        lin_correction = constrain(..., -0.3, 0.3)

        # combine linear correction and steer correction (action terms) to ensure that our mouse's motor
        # differentials are corrected, just as the slides say.
        lmot.throttle = constrain(..., -1, 1)
        rmot.throttle = constrain(..., -1, 1)

        print(angular_error, lin_error)

        time.sleep(0.05)
```
### Summary

We're implementing this portion to account for errors in distance traveled forward, this is in contrast to the last code portion which was to ensure our mouse was driving straight. We're correcting for under/overshooting the target distance by adjusting overall speed.

The linear controller provides the speed control over the motors, while the angular controller provides correction for the differential between motors. Both corrections are combined so we can simultaneously maintain straight motion AND reach the target distance.

### Checkoff #2

1. Demonstrate your working P controller. Print out your error term too.
2. How do you compute the error term?
3. If we want our applied correction power $u(t)$ to be maximized $(u(t) = 1)$ when the error is 100mm, what is $K_p$?

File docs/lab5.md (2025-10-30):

# Lab 5: Odometry and Motor Control

## Background

### Odometry

Now that we know how to read the encoders on our mouse, we can use that to estimate the position and orientation of our mouse at any given time. This is a form of *odometry*.

Why is odometry important? Suppose we want our mouse to move forward by one maze cell. We could turn on both motors for a fixed amount of time, and hope the mouse moves exactly the distance we want it to. In practice, this doesn’t work due to friction, changing battery voltage, and many other factors. The difference between the desired movement and the actual movement is called *error*, and knowing the error is the first step towards correcting it.

Using the measurements from both wheels, we can compute the odometry for the entire mouse. Our mouse is a *differential drive* robot, which means that it has two drive wheels located side by side. Both wheels turning in the same direction causes forward (or backward) motion, and both wheels turning in opposite directions causes rotation.

When we describe the position and velocity of a robot, we are actually describing the position and velocity of a single point somewhere on the robot. For a differential drive robot like our mouse, this point is usually taken to be halfway between the wheels. Since a point can’t have a rotational velocity, the “point” is actually a *coordinate frame*. You can think of a coordinate frame as a set of coordinate axes that are “attached” to the mouse and move/rotate with it.

<p align="center">
    
</p>

Consider the coordinate frame in the diagram above. When the mouse moves forward, it moves in the positive x direction. When the mouse rotates, it rotates around the z axis (which points upwards). The concept of coordinate frames is fundamental to robotics, but we won’t be able to cover it in much depth (try EECS C106A if you're interested in this type of stuff!). Fortunately, we only need to know some basics.

<p align="center">
    
</p>

We are mostly interested in the forward distance and rotational distance of our mouse. Intuitively, the center of the mouse moves with a distance that is the average of the wheel distances. Rotation in radians is arc distance divided by diameter which in our case would be the difference in wheel distances divided by the distance between the wheels. We can derive the following formulas.

<p align="center">
    $d_f = \frac{d_l + d_r}{2}$
    <br>
    $\theta = \frac{d_r - d_l}{d}$
</p>

### Motor Control

To make the mouse move, we use brushed DC motors. Applying a voltage across them makes the motor spin in one direction. Reversing this voltage makes the motor spin in the other direction.

Motors need large amounts of current and as such our Pi Pico can't drive them directly from its IO like we could with the LEDs. To solve this problem, we use the DRV8833 motor driver chip. It can drive two small motors and includes features like overcurrent protection and PWM control.

<p align="center">
    
</p>

Above is the DRV8833 breakout board we use in our mouse. One of the motors is connected to the OUT1 and OUT2 pins while the other is connected to the OUT3 and OUT4 pins. The Pi Pico is connected to the INx pins to allow it to control the corresponding OUTx pins.

Since the DRV8833 is a high power device, it needs to be powered off the 9V lithium battery included with your mouse. When using the motors, turn on the switch on your mouse to connect the battery.

To control the motors, we can reference the [datasheet](https://www.ti.com/lit/ds/symlink/drv8833.pdf). The relevant section is copied below for convenience.

<p align="center">
    
</p>

`1` means setting a pin to `True` while `0` means setting it to `False`. `Z` means the pin is "disconnected" which is also known as high impedance mode. Since we power the DRV8833 with 9V, `H` means 9V and `L` means 0V.

## Odometry

Translate the odometry equations into code by filling in the TODOs in the below code. Note that you'll first have to convert the number of encoder ticks to the actual distance traveled.

```python
import board
import time
import rotaryio
from math import pi

lenc = rotaryio.IncrementalEncoder(board.GP12, board.GP13)
renc = rotaryio.IncrementalEncoder(board.GP19, board.GP18)

ENCODER_TICKS_PER_REVOLUTION = """TODO from previous lab"""
WHEELBASE_DIAMETER = """TODO measure this in mm"""
WHEEL_DIAMETER = 34.0 # mm

while True:
    left_dist  = """TODO"""
    right_dist = """TODO"""

    dist  = """TODO"""
    theta = """TODO"""

    print(dist, theta)
    time.sleep(0.05)

```

### Checkoff #1

1. Demonstrate your working code.
2. How many millimeters does a wheel travel per encoder tick?

## Motor Control

Based on the table from the datasheet, the DRV8833 can easily put motors in forward or reverse at full power and even stop. What if we want to use a different speed? To do this we can switch between full power and stop really quickly so that we average out somewhere in between based on the proportion of time we spend in each. This is the main idea behind PWM (Pulse Width Modulation).

CircuitPython has a builtin module for this called `pwmio`. Documentation for it can be located [here](https://circuitpython.readthedocs.io/en/latest/shared-bindings/pwmio/index.html). The important values in PWM are duty cycle and frequency. Duty cycle determines the percentage of time within a cycle spent on. In the case of `pwmio`, it's a 16-bit number (0-65535). Frequency is determined by the total of the on and off times and is specified in Hertz. Since frequency determines the noise, we'll keep it at 20kHz to be at the edge of human hearing.

Look at the `pwmio` documentation and fill in the TODOs below. A duty cycle of 0 or 65535 will set a pin to be completely off or on, respectively. For reasons best explained in a nice [article](https://learn.adafruit.com/improve-brushed-dc-motor-performance/choosing-decay-mode-and-pwm-frequency), we want to switch between the forward and slow decay states of the DRV8833 for PWM.

 Try different variations, keeping in1's duty cycle the same (high), begin from a low value for in2, what do you notice as you increase?

```python
import board
import pwmio

lmot_in1 = """TODO create PWMOut object on pin GP16 at 20kHz"""
lmot_in2 = """TODO create PWMOut object on pin GP17 at 20kHz"""

while True:
    lmot_in1.duty_cycle = """TODO set to 25% speed forward should be an int"""
    lmot_in2.duty_cycle = """TODO set to 25% speed forward should be an int"""
```

### Checkoff #2

1. Demonstrate your left wheel spinning forward at 25% speed.
2. What happens if we swap the two PWM pins?

## Motor Control w/ Library

Having to deal with PWM outputs and duty cycles can get tedious. As is usually the case, CircuitPython provides a nice library named `motor` for this very thing. Read the [documentation](https://circuitpython.readthedocs.io/projects/motor/en/latest/api.html), specifically check out the throttle function, and fill out the TODOs in the following code. If you are having trouble refer to the code in sanity for a nice helpful guide! 

```python
import board
import time
import pwmio
import adafruit_motor.motor as motor

"""TODO don't forget to make PWMOut objects first"""

lmot = """TODO create DCMotor object on pins GP16 and GP17"""
rmot = """TODO create DCMotor object on pins GP15 and GP14""" 

"""TODO set lmot and rmot to SLOW_DECAY"""

while True:
    """TODO move full speed forward for 1s"""

    """TODO brake for 1s"""

    """TODO move 25% speed backward for 1s"""

    """TODO brake for 1s"""
```

### Checkoff #3

1. Demonstrate your code is working.
2. What happens if we pass a `throttle` value larger than 1.0 or -1.0?
3. SAVE YOUR CODE YOULL NEED IT FOR NEXT LAB

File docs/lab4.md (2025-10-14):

# Lab 4: IR Sensors
Note to staff: we changed the order. Refer to Harri's old version if your curious
## Background

IR sensors work by sending out IR light and measuring the amount reflected back. They take a lot more work to calibrate and are surface dependent, but are far cheaper and faster than the ToF sensors we used to use. Our mouse has 6 of these sensors split into 3 pairs (center/front, left, right). Having 2 sensors per side allows us to statically determine both the distance and angle of the nearest surface.

IR sensors consist of both an IR emitter and detector. IR emitters draw around 50mA each when on, so we have a switch to turn them off when not needed. IR detectors shift their IV curve based on light intensity like in the following graph.

<p align="center">
    
</p>

To convert that to a readable voltage signal, we'll use a setup similar to a resistor divider. It's noisier and less tunable compared to a transimpedance amplifier, but uses only one resistor. By placing the IR detector in reverse bias, we use the flatter region of the IV curve. Since the current varies linearly with light intensity, the voltage also varies linearly. MMv3 uses the following circuit (pull-up resistor not shown).

<p align="center">
    
</p>

## Read One Sensor

Since we have 6 total analog sensors but only 3 ADC pins on the Pi Pico, we need to multiplex 2 sensors onto each pin. We use one extra pin on each IR detector in open-drain mode to fully disconnect or connect it to ground. To read in one sensor, we perform the following steps in the while loop.

1. Enable the IR emitters (set pin to `True`).
2. Enable the chosen sensor by connecting it to ground (set pin to `False`).
3. Wait around 1ms for things to settle.
4. Take the reading.
5. Disable the chosen sensor by setting the pin to open-drain (set pin to `True`).
6. Disable the IR emitters (set pin to `False`).

Baesd on the above steps, the `AnalogIn` [documentation](https://circuitpython.readthedocs.io/en/latest/shared-bindings/analogio/index.html), and the `DigitalInOut` [documentation](https://docs.circuitpython.org/en/latest/shared-bindings/digitalio/) fill out the below TODOs to print out readings from the left IR sensor pair (`lir_a` and `lir_b`).

```python
import board
import time
import digitalio
from analogio import AnalogIn

# adc 
l_adc = """TODO call AnalogIn on GP28"""

# emitter 
l_en = """TODO create DigitalInOut output on GP7"""
l_en.direction = digitalio.Direction.OUTPUT
l_en.value = False

# sensors
lir_a = digitalio.DigitalInOut(board.GP5)
lir_a.direction = digitalio.Direction.OUTPUT
lir_a.drive_mode = digitalio.DriveMode.OPEN_DRAIN
lir_a.value = True # high Z mode

lir_b = """TODO create DigitalInOut on GP6 in open-drain mode, use lir_a as direct inspiration"""
lir_b.direction  = ...
lir_b.drive_mode = ...
lir_b.value = ...

while True:
    # TODO enable IR emitters using l_en set one of its variables to a (boolean)

    # TODO enable chosen sensor lir_a or lir_b by setting one of its variable to false
    # TODO wait a bit, 1ms should do time. ...
    # TODO take analog reading for future printing print(l_adc. , end=" ")
    # TODO disable chosen sensor lir_a or lir_b 

    # TODO try for lir_b or lir_a whichever one you didnt use instead, enable chosen sensor etc
    # Repeat above for this sensor

    # TODO disable IR emitters using l_en 
    time.sleep(0.05)
```

### Checkoff #1

1. Demonstrate one working sensor.

### Summary 
You should have now read from your lir_a and lir_b sensors and have printed to your screen their values. Fun fact the time it takes for a pixel to be displayed to your screen is longer than the time it takes to send a byte from LA to NYC!

## Read All the Sensors

In order to simplify the whole process of multiplexing and reading from multiple sensors, we wrote a library. Upload, if you havent already `irsensor.py` from [sanity/](../labs/sanity), to serve as the library. Read through `irsensor.py` to instantiate and use it to understand the parameters of IRSensors. You can paste this over your prior code.py.

```python
import board
import time

from irsensor import IRSensors

ir = IRSensors(
    board.GP7,  board.GP5,  board.GP6,  board.GP28, # left
    board.GP9,  board.GP10, board.GP11, board.GP26, # center
    board.GP21, board.GP20, board.GP22, board.GP27  # right
)

while True:
    ir.scan()
    print("lir_a:", ir.lir_a, "\t", "lir_b:", ir.lir_b, "\t",
            "cir_a:", ir.cir_a, "\t", "cir_b:", ir.cir_b, "\t",
            "rir_a:", ir.rir_a, "\t", "rir_b:", ir.rir_b)
    time.sleep(0.05)
```

### Checkoff #2

1. Demonstrate all of your working sensors.

### Summary
This should appear similar to what you saw from sanity :)

## Calibration

Let's try estimating actual distances from the sensor values. Empirically, the relationship is linear below around 60mm and rises sharply beyond that due to the angled sensors seeing above the wall. Based on maze cell size, we really only need accurate distances around 50mm (~2in) for wall following and just binary wall detection beyond that.

<p align="center">
    
    <br>
    <a><b>IR Sensor Linear Region</b></a>
</p>

Load up [`code.py`](../labs/lab4/code.py) which contains code to automate finding the constants. You'll be using a maze wall and ruler to take readings at various distances. The code then uses least squares to determine constants for fitting the line to the points and prints out the constants at the end. The equation using these constants to convert sensor readings to distances can be expressed as follows.

<p align="center">
    $distance = a \cdot sensor + b$
</p>

To save you some time, we're also going to include code for you to get proper distance readings: [`distance.py`](../labs/lab4/distance.py). 
Pay attention to this area specifically: 

```python
# IR sensors
ir = IRSensors(
    board.GP7,  board.GP5,  board.GP6,  board.GP28, # left
    board.GP9,  board.GP10, board.GP11, board.GP26, # center
    board.GP21, board.GP20, board.GP22, board.GP27, # right
    avg = 10
)

""" Main """

''' Please ensure you change these to your own, these are for another mouse'''
dist = Distance(ir,
    0.0299, -63.6, 0.0195, -39.1,
    0.0300, -60.4, 0.0251, -47.9,
    0.0258, -50.5, 0.0292, -54.0,
)

"""Make Sure to allign the constants in the right place:
        la_a, la_b, lb_a, lb_b,
        ca_a, ca_b, cb_a, cb_b,
        ra_a, ra_b, rb_a, rb_b,
"""
```

Within the file we make an instance of the Distance class and passing in the arguments for the __a__ and __b__ constants. The numbers given out are placeholders and you should use the constants you got from the previous section and fill them in appropriately. 

### Checkoff #3

1. Run the calibration code and save the constants somewhere.
2. Using the constants, fill in the distance code and check that it runs correctly.

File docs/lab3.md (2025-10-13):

# Lab 3: Encoders

## Background

When we're navigating the maze, we'd like to keep track of a couple things.

* Is it driving straight?
* How far has it driven?
* What direction is it facing?

To answer these questions, we'll use the **quadrature encoder** sensors mounted on the back of your motors. They consist of a spinning magnet and two Hall effect sensors mounted 90° apart. Hall effect sensors measure the presence of magnetic fields. In our case, they output a `True` when closer to a north pole and `False` when closer to a south pole.

<p align="center">
    
    <br>
    <a><b>Hall sensor signal (y-axis) vs. time (x-axis)</b></a>
</p>

## Waveform Viewing

Let's try reading raw values from the encoder. Upload the following code.

```python
import board
import time
import digitalio

# a and b Hall effect sensors of left encoder
a = digitalio.DigitalInOut(board.GP12)
b = digitalio.DigitalInOut(board.GP13)

while True:
    print(int(a.value), int(b.value))
    time.sleep(0.001)
```

Pull up a serial monitor and start spinning the left motor at various speeds. Notice how the values start changing. Can you tell which direction the motor is spinning with just one input?

### Checkoff #1

1. What's the output when the motor is stationary? Is it a certain level? Is it constant?
2. How does the output change when you spin the motor faster?
3. Why do we need two Hall effect sensors per motor?

## Polling

Next let's try tracking the position of the left wheel. We're going to use a technique called polling which involves repeatedly reading a signal to detect changes. Fill in the `leftEncoderRisingEdge` function below. When would we want to detect rising edges? For which channel? Refer to the [slides](https://docs.google.com/presentation/d/1K-QloCbwE4FLP0DOvIL4pT_rOTX5n5soy-6r5Pd3Yes/edit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) Think about how the output looked like in the sanity lab we did! We want a similar process here. Your solution can be one line with python syntactic sugar :) 

```python
import board
import digitalio

# a and b Hall effect sensors of left encoder
a = digitalio.DigitalInOut(board.GP12)
b = digitalio.DigitalInOut(board.GP13)

counter = 0
position = 0
a_prev = a.value

def leftEncoderRisingEdge():
    """TODO increment or decrement position depending on which way the motor is spinning
    Try experimenting with the instance variables of a and b (we only need either a or b). Refer to the
    waveform code from earlier for an idea, think about rising edges"""
    global position # access global position
    if b.value == ... : # can be simplified lol
        position += ...
    else:
        ...

while True:
    a_val = a.value
    if a_val and not a_prev: # rising edge of a
        leftEncoderRisingEdge()
    a_prev = a_val

    if counter % 1000 == 0:
        print(position)
    counter += 1
```

After uploading the code, pull up a serial monitor and start spinning the motor in both directions. The position should go up and down as you do it!

### Checkoff #2

1. Show your working code.
2. Roughly how many "ticks" correspond to a revolution? How do you think this is computed?
3. What issues might the "polling" method have?
4. Now that we can measure position, how might we measure velocity?
5. What effect does swapping the A and B pins have on how we measure position?

## Interrupts

Polling can be inefficient and even miss edges if the wheel is spinning too quickly. Moreover, constantly having to check a signal takes up a lot of CPU time that could be used for other purposes. While polling is adequate in some cases, for an encoder we need something better.

Interrupts literally interrupt the CPU by making it pause its current task and run some other code before resuming. In our case, we want to trigger an interrupt when a pin has a rising edge. The low-level setup for interrupts usually involves enabling some registers and assigning a function to run. CircuitPython actually abstracts all of this away for us in the `rotaryio` module.

Upload the following code.

```python
import board
import time
import rotaryio

enc = rotaryio.IncrementalEncoder(board.GP12, board.GP13)

while True:
    print(enc.position)
    time.sleep(0.001)
```

Pull up a serial monitor and start spinning the motor.

### Checkoff #3

1. Demonstrate the working code.
2. Why might we use interrupts over polling?

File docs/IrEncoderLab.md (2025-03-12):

# Lab 3: Sensory Overload 

## Background

Originally, this entire lab consisted of two labs total: IR sensing and Encoders. Now we've merged them into two for your enjoyment and hopefully ease-of-learning. We're gonna start with encoders and then move to IR sensors.
# Encoders 
## Background

When we're navigating the maze, we'd like to keep track of a couple things.

* Is it driving straight?
* How far has it driven?
* What direction is it facing?

To answer these questions, we'll use the **quadrature encoder** sensors mounted on the back of your motors. They consist of a spinning magnet and two Hall effect sensors mounted 90° apart. Hall effect sensors measure the presence of magnetic fields. In our case, they output a `True` when closer to a north pole and `False` when closer to a south pole.

<p align="center">
    
    <br>
    <a><b>Hall sensor signal (y-axis) vs. time (x-axis)</b></a>
</p>

## Waveform Viewing

Let's try reading raw values from the encoder. Upload the following code.

```python
import board
import time
import digitalio

# a and b Hall effect sensors of left encoder
a = digitalio.DigitalInOut(board.GP12)
b = digitalio.DigitalInOut(board.GP13)

while True:
    print(int(a.value), int(b.value))
    time.sleep(0.001)
```

Pull up a serial monitor and start spinning the left motor at various speeds. Notice how the values start changing. Can you tell which direction the motor is spinning with just one input?

### Checkoff #1

1. What's the output when the motor is stationary? Is it a certain level? Is it constant?
2. How does the output change when you spin the motor faster?
3. Why do we need two Hall effect sensors per motor?

## Polling

Next let's try tracking the position of the left wheel. We're going to use a technique called polling which involves repeatedly reading a signal to detect changes. Fill in the `leftEncoderRisingEdge` function below.

```python
import board
import digitalio

# a and b Hall effect sensors of left encoder
a = digitalio.DigitalInOut(board.GP12)
b = digitalio.DigitalInOut(board.GP13)

counter = 0
position = 0
a_prev = a.value

def leftEncoderRisingEdge():
    global position # access global position
    """TODO increment or decrement position depending on which way the motor is spinning
    Try experimenting with the instance variables of a and b (we only need either a or b). Refer to the
    waveform code from earlier for an idea, think about rising edges"""

while True:
    a_val = a.value
    if a_val and not a_prev: # rising edge of a
        leftEncoderRisingEdge()
    a_prev = a_val

    if counter % 1000 == 0:
        print(position)
    counter += 1
```

After uploading the code, pull up a serial monitor and start spinning the motor in both directions. The position should go up and down as you do it!

### Checkoff #2

1. Show your working code.
2. Roughly how many "ticks" correspond to a revolution? How do you think this is computed?
3. What issues might the "polling" method have?
4. Now that we can measure position, how might we measure velocity?
5. What effect does swapping the A and B pins have on how we measure position?

## Interrupts

Polling can be inefficient and even miss edges if the wheel is spinning too quickly. Moreover, constantly having to check a signal takes up a lot of CPU time that could be used for other purposes. While polling is adequate in some cases, for an encoder we need something better.

Interrupts literally interrupt the CPU by making it pause its current task and run some other code before resuming. In our case, we want to trigger an interrupt when a pin has a rising edge. The low-level setup for interrupts usually involves enabling some registers and assigning a function to run. CircuitPython actually abstracts all of this away for us in the `rotaryio` module.

Upload the following code.

```python
import board
import time
import rotaryio

enc = rotaryio.IncrementalEncoder(board.GP12, board.GP13)

while True:
    print(enc.position)
    time.sleep(0.001)
```

Pull up a serial monitor and start spinning the motor.

### Checkoff #3

1. Demonstrate the working code.
2. Why might we use interrupts over polling?

# IR Sensors

IR sensors work by sending out IR light and measuring the amount reflected back. They take a lot more work to calibrate and are surface dependent, but are far cheaper and faster than the ToF sensors we used to use. Our mouse has 6 of these sensors split into 3 pairs (center/front, left, right). Having 2 sensors per side allows us to statically determine both the distance and angle of the nearest surface.

IR sensors consist of both an IR emitter and detector. IR emitters draw around 50mA each when on, so we have a switch to turn them off when not needed. IR detectors shift their IV curve based on light intensity like in the following graph.

<p align="center">
    
</p>

To convert that to a readable voltage signal, we'll use a setup similar to a resistor divider. It's noisier and less tunable compared to a transimpedance amplifier, but uses only one resistor. By placing the IR detector in reverse bias, we use the flatter region of the IV curve. Since the current varies linearly with light intensity, the voltage also varies linearly. MMv3 uses the following circuit (pull-up resistor not shown).

<p align="center">
    
</p>

## Read One Sensor

Since we have 6 total analog sensors but only 3 ADC pins on the Pi Pico, we need to multiplex 2 sensors onto each pin. We use one extra pin on each IR detector in open-drain mode to fully disconnect or connect it to ground. To read in one sensor, we perform the following steps.

1. Enable the IR emitters (set pin to `True`).
2. Enable the chosen sensor by connecting it to ground (set pin to `False`).
3. Wait around 1ms for things to settle.
4. Take the reading.
5. Disable the chosen sensor by setting the pin to open-drain (set pin to `True`).
6. Disable the IR emitters (set pin to `False`).

Baesd on the above steps and the `AnalogIn` [documentation](https://circuitpython.readthedocs.io/en/latest/shared-bindings/analogio/index.html), fill out the below TODOs to print out readings from the left IR sensor pair (`lir_a` and `lir_b`).

```python
import board
import time
import digitalio
from analogio import AnalogIn

# adc
l_adc = """TODO create AnalogIn on GP28"""

# emitter
l_en = """TODO create DigitalInOut output on GP7"""
l_en.direction = digitalio.Direction.OUTPUT
l_en.value = False

# sensors
lir_a = digitalio.DigitalInOut(board.GP5)
lir_a.direction = digitalio.Direction.OUTPUT
lir_a.drive_mode = digitalio.DriveMode.OPEN_DRAIN
lir_a.value = True # high Z mode

lir_b = """TODO create DigitalInOut on GP6 in open-drain mode, use lir_a as direct inspiration"""

while True:
    # TODO enable IR emitters using l_en set one of its variables to a (boolean)

    # TODO enable chosen sensor lir_a or lir_b by setting one of its variable to false
    # TODO wait a bit, 1ms should do time. ...
    # TODO take analog reading for future printing print(l_adc. , end="")
    # TODO disable chosen sensor lir_a or lir_b 

    # TODO enable chosen sensor
    #
    # Repeat above for this sensor
    #
    # TODO disable IR emitters using l_en
    time.sleep(0.05)
```

### Checkoff #1

1. Demonstrate one working sensor.

## Read All the Sensors

In order to simplify the whole process of multiplexing and reading from multiple sensors, we wrote a library. Upload `irsensor.py` from [sanity/](../labs/sanity) to serve as the library. We've provided the code below to allow all IR sensors to take measurements. Run the code below to make sure every sensor works!

```python
import board
import time

from irsensor import IRSensors

ir = IRSensors(
    board.GP7,  board.GP5,  board.GP6,  board.GP28, # left
    board.GP9,  board.GP10, board.GP11, board.GP26, # center
    board.GP21, board.GP20, board.GP22, board.GP27  # right
)

while True:
    ir.scan()
    print("lir_a:", ir.lir_a, "\t", "lir_b:", ir.lir_b, "\t",
            "cir_a:", ir.cir_a, "\t", "cir_b:", ir.cir_b, "\t",
            "rir_a:", ir.rir_a, "\t", "rir_b:", ir.rir_b)
    time.sleep(0.05)
```

### Checkoff #2

1. Demonstrate all of your working sensors.

## Calibration

Let's try estimating actual distances from the sensor values. Empirically, the relationship is linear below around 60mm and rises sharply beyond that due to the angled sensors seeing above the wall. Based on maze cell size, we really only need accurate distances around 50mm for wall following and just binary wall detection beyond that.

<p align="center">
    
    <br>
    <a><b>IR Sensor Linear Region</b></a>
</p>

Load up [`constants.py`](../labs/lab4/constants.py) which contains code to automate finding the constants. You'll be using a maze wall and ruler to take readings at various distances. The code then uses least squares to fit a line to the points and prints out the constants at the end. The equation using these constants to convert sensor readings to distances can be expressed as follows.

<p align="center">
    $distance = a \cdot sensor + b$
</p>

To save you some time, we're also going to include code for you to get proper distance readings: [`distance.py`](../labs/lab4/distance.py). 
Pay attention to this area specifically: 

```python
# IR sensors
ir = IRSensors(
    board.GP7,  board.GP5,  board.GP6,  board.GP28, # left
    board.GP9,  board.GP10, board.GP11, board.GP26, # center
    board.GP21, board.GP20, board.GP22, board.GP27, # right
    avg = 10
)

""" Main """

dist = Distance(ir,
    0.0299, -63.6, 0.0195, -39.1,
    0.0300, -60.4, 0.0251, -47.9,
    0.0258, -50.5, 0.0292, -54.0,
)

"""Make Sure to allign the constants in the right place:
        la_a, la_b, lb_a, lb_b,
        ca_a, ca_b, cb_a, cb_b,
        ra_a, ra_b, rb_a, rb_b,
"""
```

Within the file we make an instance of the Distance class and passing in the arguments for the __a__ and __b__ constants. The numbers given out are placeholders and you should use the constants you got from the previous section and fill them in appropriately. 

### Checkoff #3

1. Run the calibration code and save the constants somewhere.
2. Using the constants, fill in the distance code and check that it runs correctly.

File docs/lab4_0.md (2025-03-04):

# Lab 4: IR Sensors
Note to staff: we changed the order
## Background

IR sensors work by sending out IR light and measuring the amount reflected back. They take a lot more work to calibrate and are surface dependent, but are far cheaper and faster than the ToF sensors we used to use. Our mouse has 6 of these sensors split into 3 pairs (center/front, left, right). Having 2 sensors per side allows us to statically determine both the distance and angle of the nearest surface.

IR sensors consist of both an IR emitter and detector. IR emitters draw around 50mA each when on, so we have a switch to turn them off when not needed. IR detectors shift their IV curve based on light intensity like in the following graph.

<p align="center">
    
</p>

To convert that to a readable voltage signal, we'll use a setup similar to a resistor divider. It's noisier and less tunable compared to a transimpedance amplifier, but uses only one resistor. By placing the IR detector in reverse bias, we use the flatter region of the IV curve. Since the current varies linearly with light intensity, the voltage also varies linearly. MMv3 uses the following circuit (pull-up resistor not shown).

<p align="center">
    
</p>

## Read One Sensor

Since we have 6 total analog sensors but only 3 ADC pins on the Pi Pico, we need to multiplex 2 sensors onto each pin. We use one extra pin on each IR detector in open-drain mode to fully disconnect or connect it to ground. To read in one sensor, we perform the following steps.

1. Enable the IR emitters (set pin to `True`).
2. Enable the chosen sensor by connecting it to ground (set pin to `False`).
3. Wait around 1ms for things to settle.
4. Take the reading.
5. Disable the chosen sensor by setting the pin to open-drain (set pin to `True`).
6. Disable the IR emitters (set pin to `False`).

Baesd on the above steps and the `AnalogIn` [documentation](https://circuitpython.readthedocs.io/en/latest/shared-bindings/analogio/index.html), fill out the below TODOs to print out readings from the left IR sensor pair (`lir_a` and `lir_b`).

```python
import board
import time
import digitalio
from analogio import AnalogIn

# adc
l_adc = """TODO create AnalogIn on GP28"""

# emitter
l_en = """TODO create DigitalInOut output on GP7"""
l_en.direction = digitalio.Direction.OUTPUT
l_en.value = False

# sensors
lir_a = digitalio.DigitalInOut(board.GP5)
lir_a.direction = digitalio.Direction.OUTPUT
lir_a.drive_mode = digitalio.DriveMode.OPEN_DRAIN
lir_a.value = True # high Z mode

lir_b = """TODO create DigitalInOut on GP6 in open-drain mode, use lir_a as direct inspiration"""

while True:
    # TODO enable IR emitters using l_en
    # TODO enable chosen sensor lir_a or lir_b
    # TODO wait a bit, 1ms should do
    # TODO take analog reading for future printing
    # TODO disable chosen sensor lir_a or lir_b
    # TODO disable IR emitters using l_en
    time.sleep(0.05)
```

### Checkoff #1

1. Demonstrate one working sensor.

## Read All the Sensors

In order to simplify the whole process of multiplexing and reading from multiple sensors, we wrote a library. Upload `irsensor.py` from [sanity/](../labs/sanity) to serve as the library. Read through `irsensor.py` to instantiate and use it and fill out the below TODOs to print out all sensor readings in real time.

```python
import board
import time

from irsensor import IRSensors

ir = IRSensors(
    """TODO sensor | en   | a    | b    | adc"""
    """TODO lir    | GP7  | GP5  | GP6  | GP28"""
    """TODO cir    | GP9  | GP10 | GP11 | GP26"""
    """TODO rir    | GP21 | GP20 | GP22 | GP27"""
)

while True:
    """TODO get and print all sensor readings"""
    time.sleep(0.05)
```

### Checkoff #2

1. Demonstrate all of your working sensors.

## Calibration

Let's try estimating actual distances from the sensor values. Empirically, the relationship is linear below around 60mm and rises sharply beyond that due to the angled sensors seeing above the wall. Based on maze cell size, we really only need accurate distances around 50mm for wall following and just binary wall detection beyond that.

<p align="center">
    
    <br>
    <a><b>IR Sensor Linear Region</b></a>
</p>

Load up [`code.py`](../labs/lab4/code.py) which contains code to automate finding the constants. You'll be using a maze wall and ruler to take readings at various distances. The code then uses least squares to fit a line to the points and prints out the constants at the end. The equation using these constants to convert sensor readings to distances can be expressed as follows.

<p align="center">
    $distance = a \cdot sensor + b$
</p>

### Checkoff #3

1. Run the calibration code and save the constants somewhere.
2. Using the constants, write code to convert sensor values to distances.

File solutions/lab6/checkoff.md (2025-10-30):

# Lab 6 Checkoff Solutions

## Checkoff #1

1. See that the mouse drives straight. Our motors are actually pretty consistent so the difference may not be obvious. The angular error doesn't actually need to go to 0 since we're measuring distance not velocity. It just needs to be stable. Also take a look at their code since this is the first time there's a decent amount of it. Try to encourage them towards clean and readable code. Solution code is in [chk1_code.py](chk1_code.py).
2. Some combination of a target theta minus the actual theta. They could just say theta, but make sure say we can generalize to any desired theta.
```python
left_dist  = lenc.position * MM_PER_TICK
right_dist = renc.position * MM_PER_TICK

theta = (right_dist - left_dist) / WHEELBASE_DIAMETER
theta_target = 0

e_ang = theta_target - theta    # This is the error term
```

3. $K_p = 0.5$

Why? What do we know? 

$$ u(t) = error * K_p $$

$$ error = 2 rad $$

$$ u(t) = 1 $$

Let's plug in what we know to find our unknown, $K_p$

$$ 1 = 2 rad * K_p $$

$$ K_p = 1 / 2 $$

(P.S. don't mind the dropping of the units radian, idk why tbh)

4. Too low and it corrects too slowly or not at all. Too high and it might oscillate and go unstable.

## Checkoff #2

1. See that the mouse drives straight and stops after around 20cm. Don't worry too much about extreme precision. Solution code is in [chk2_code.py](chk2_code.py).
2. Some combination of a target distance minus the current distance.
```python
dist  = (left_dist + right_dist) / 2
dist_target = 200

e_lin = dist_target - dist  # This is the error term
```
3. $K_p = 0.01$

Why? What do we know? 

$$ u(t) = error * K_p, error = 100mm, u(t) = 1 $$

Let's plug in what we know to find our unknown, $K_p$

$$ 1 = 100 * K_p $$

$$ K_p = 1 / 100 $$

(P.S. don't mind the dropping of the units radian, idk why tbh)

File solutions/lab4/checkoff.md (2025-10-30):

# Lab 4 IR Section
## Checkoff #1

1. Just looking to see if the readings are good and consistent with other mice. If not, they might have trouble later.

```python
import board
import time
import digitalio
from analogio import AnalogIn

l_en  = digitalio.DigitalInOut(board.GP7)
l_en.direction = digitalio.Direction.OUTPUT
l_en.value = False
l_adc = AnalogIn(board.GP28)

lir_a   = digitalio.DigitalInOut(board.GP5)
lir_a.direction  = digitalio.Direction.OUTPUT
lir_a.drive_mode = digitalio.DriveMode.OPEN_DRAIN
lir_a.value = True # high Z mode

lir_b   = digitalio.DigitalInOut(board.GP6)
lir_b.direction  = digitalio.Direction.OUTPUT
lir_b.drive_mode = digitalio.DriveMode.OPEN_DRAIN
lir_b.value = True # high Z mode

while True:
    l_en.value = True

    lir_a.value = False
    time.sleep(0.001)
    print(l_adc.value, end=" ")
    lir_a.value = True

    lir_b.value = False
    time.sleep(0.001)
    print(l_adc.value)
    lir_b.value = True

    l_en.value = False

    time.sleep(0.05)
```

## Checkoff #2

1. Verify all sensors are in working order

## Checkoff #3

1. Just check that they ran the code and have reasonable looking constants. The slope tends to be the same with a slight difference in offset. Around `a=0.03` and `b=-50` appear to be the average.
2. This involves combining taking the sensor readings from the previous checkpoint and implementing the provided equation. The file provided to students is also an example solution so it should work properly. 

# Encoder Section

## Checkoff #1

1. Values are constant.
2. It toggles between 0 and 1 faster.
3. To tell direction. Waveform looks the same forward and backward with just one.

## Checkoff #2

1. There's a couple of ways to do it, but here's one.

```python
import board
import digitalio

# left encoder
a = digitalio.DigitalInOut(board.GP12)
b = digitalio.DigitalInOut(board.GP13)

counter = 0
position = 0
a_prev = a.value

def leftEncoderRisingEdge():
    global position # access global position
    position += 1 if b.value else -1

while True:
    a_val = a.value
    if a_val and not a_prev: # rising edge
        leftEncoderRisingEdge()
    a_prev = a_val

    if counter % 1000 == 0:
        print(position)
    counter += 1
```

2. About 217. Multiply the gearbox ratio by the number of north poles on the motor magnet.
3. Basically can miss edges and takes up too much CPU time.
4. Use a timer to measure time between edges.
5. Just reverses the direction of measurement.

## Checkoff #3

1. Does it go up and down.
2. Interrupts don't miss edges and don't need the CPU constantly reading. There's still a limit on speed bc of interrupt and function overhead.

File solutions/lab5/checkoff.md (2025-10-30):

# Lab 5 Odometry Checkoff Solutions

## Checkoff #1

1. Have them manually move the mouse straight and see if the distance roughly matches. Then have them rotate in place and see if the angle matches.

```python
import board
import time
import rotaryio
from math import pi

lenc = rotaryio.IncrementalEncoder(board.GP12, board.GP13)
renc = rotaryio.IncrementalEncoder(board.GP19, board.GP18)

ENCODER_TICKS_PER_REVOLUTION = 217
WHEELBASE_DIAMETER = 78.0 # mm
WHEEL_DIAMETER = 34.0 # mm

while True:
    MM_PER_TICK = pi * WHEEL_DIAMETER / ENCODER_TICKS_PER_REVOLUTION
    left_dist  = lenc.position * MM_PER_TICK
    right_dist = renc.position * MM_PER_TICK

    dist  = (left_dist + right_dist) / 2
    theta = (right_dist - left_dist) / WHEELBASE_DIAMETER

    print(dist, theta)
    time.sleep(0.05)
```

2. About 0.5mm

## Checkoff #2

1. Just needs to be moving at somewhat low speed. Run the code below to get a feel for it. Don't worry about direction. The biggest gotcha is that the IN2 pin needs to be on 75% of the time instead of 25% to get 25% speed.

```python
import board
import pwmio

lmot_in1 = pwmio.PWMOut(board.GP16, frequency=20000)
lmot_in2 = pwmio.PWMOut(board.GP17, frequency=20000)

while True:
    lmot_in1.duty_cycle = 65535
    lmot_in2.duty_cycle = 49151
```

2. Motor direction will reverse.

## Checkoff #3

1. Make sure it does motions specified in the TODOs.

```python
import board
import time
import pwmio
import adafruit_motor.motor as motor

lmot = motor.DCMotor(
    pwmio.PWMOut(board.GP16, frequency=20000),
    pwmio.PWMOut(board.GP17, frequency=20000)
)
rmot = motor.DCMotor(
    pwmio.PWMOut(board.GP15, frequency=20000),
    pwmio.PWMOut(board.GP14, frequency=20000)
)
lmot.decay_mode = motor.SLOW_DECAY
rmot.decay_mode = motor.SLOW_DECAY

while True:
    lmot.throttle, rmot.throttle = 1, 1
    time.sleep(1)
    lmot.throttle, rmot.throttle = 0, 0
    time.sleep(1)
    lmot.throttle, rmot.throttle = -0.25, -0.25
    time.sleep(1)
    lmot.throttle, rmot.throttle = 0, 0
    time.sleep(1)
```

2. It throws an error. Let them know that means we need to keep values within the valid range for future labs.

Wanna make your mouse turn? If you want to run this without being connected remember to include the main statement!

```python
import board
import pwmio

lmot_in1 = pwmio.PWMOut(board.GP16, frequency=20000)
lmot_in2 = pwmio.PWMOut(board.GP17, frequency=20000)

rmot_in1 = pwmio.PWMOut(board.GP15, frequency=20000)
rmot_in2 = pwmio.PWMOut(board.GP14, frequency=20000)

while True:
    lmot_in1.duty_cycle = 49151
    lmot_in2.duty_cycle = 65535

    rmot_in1.duty_cycle = 65535 
    rmot_in2.duty_cycle = 49151
```

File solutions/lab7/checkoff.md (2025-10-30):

# Lab 7 Checkoff Solutions

## Checkoff #1

1. Remember Riemann sums from calculus? Basically we just add up the measured error over time. Technically we're supposed to multiply by dt, but that's just a scalar error.
2. Go back to the definition of derivative. Basically we take the difference between our current error and previous error. Technically we're supposed to divide by dt, but that again a scalar error.
3. The main idea is that we limit the size of the integral term. A good limit is whatever value of the integral term causes the maximum power to be put into the motor.

## Checkoff #2

1. As long as it drives straight 200mm and stops like in Lab 5, it's good.
2. As long as it turns in place about 90° and stops, it's good.
3. As long as it turns in place about 90° and stops for one second and keeps doing that, it's good. Solution code is in [chk2_code.py](chk2_code.py).
4. They should mention some concept of adding up an error over time. Addressing integral windup by constraining the summation's value is highly recommended, but not necessary.

## Checkoff #3

1. Make sure that the mouse maintains roughly a constant distance from the wall and drives parallel. It should move forward 180mm and stop every second. Solution code is in [chk3_code.py](chk3_code.py).
2. Swap the fixed distance with the right sensor's reading. There are some extra considerations since the angle from both walls are not independent but that's the main idea.

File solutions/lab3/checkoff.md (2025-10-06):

# Lab 3 Checkoff Solutions NOTE THIS IS FOR IR WE SWITCHED THE ORDER

## Checkoff #1

1. Just looking to see if the readings are good and consistent with other mice. If not, they might have trouble later.

```python
import board
import time
import digitalio
from analogio import AnalogIn

# adc
l_adc = AnalogIn(board.GP28)

#emitter 
l_en  = digitalio.DigitalInOut(board.GP7)
l_en.direction = digitalio.Direction.OUTPUT
l_en.value = False

# sensors
lir_a   = digitalio.DigitalInOut(board.GP5)
lir_a.direction  = digitalio.Direction.OUTPUT
lir_a.drive_mode = digitalio.DriveMode.OPEN_DRAIN
lir_a.value = True # high Z mode

# STUDENT DO THIS
lir_b   = digitalio.DigitalInOut(board.GP6)
lir_b.direction  = digitalio.Direction.OUTPUT
lir_b.drive_mode = digitalio.DriveMode.OPEN_DRAIN
lir_b.value = True # high Z mode

while True:
    l_en.value = True

    lir_a.value = False
    time.sleep(0.001)
    print(l_adc.value, end=" ")
    lir_a.value = True

    lir_b.value = False
    time.sleep(0.001)
    print(l_adc.value)
    lir_b.value = True

    l_en.value = False

    time.sleep(0.05)
```

## Checkoff #2

In order to simplify the whole process of multiplexing and reading from multiple sensors, we wrote a library. Upload, if you havent already irsensor.py from sanity/, to serve as the library. Read through irsensor.py to instantiate and use it to understand the parameters of IRSensors.

1. Verify all sensors are in working order

## Checkoff #3

1. Just check that they ran the code and have reasonable looking constants. The slope tends to be the same with a slight difference in offset. Around `a=0.03` and `b=-50` appear to be the average.
2. This involves combining taking the sensor readings from the previous checkpoint and implementing the provided equation. The file provided to students is also an example solution so it should work properly.

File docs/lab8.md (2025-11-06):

# Lab 8: Maze Solving Primitives 

You now have all the tools to work on maze solving. The simplest implementation is to just have `forward`, `turn_left`, `turn_right`, and `turn_around` functions. Turning should be pretty easy, but implementing `forward` is trickier as it needs to wall follow, account for lack of walls to reference, and correct for distance errors. Here's some considerations.

- There are 8 possible cases on wall presence for `forward` bc there are 4 walls in consideration when moving forward one cell.
- If we suddenly see an opening on the left or right (or sudden appearance of a wall) we can correct our internal distance measurement.
- We want to maintain 0° with respect to wall on left and right which means an error for each side. If we see openings on the left and right, the errors will point in opposite directions and we should drive straight using just encoders.
- If we start without a wall on one side, we should wall follow using just the other side. May be a concern if that side suddenly lacks a wall so perhaps just drive straight using encoders.
- Should take the minimum of the efforts to correct for both wall angle errors to account for suddenly seeing an opening on one side.
- How can we keep track of the mouses, state, that is how can we create a physical representation of the system relative to our mouse position.

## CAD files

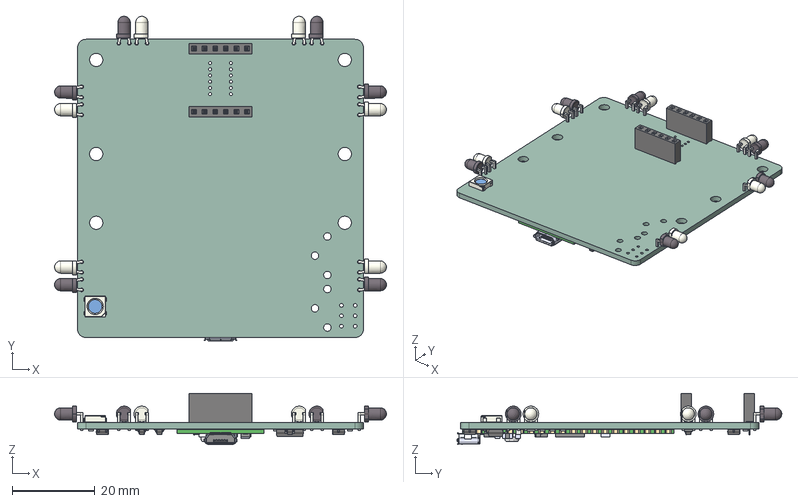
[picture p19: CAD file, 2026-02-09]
board/MMv3.step
80.1 x 78.4 x 12.4 mm
LED_WS2812B_PLCC4_50x50mm_P32mm
LED_D3.0mm_Horizontal_O1.27mm_Z2.0mm_IRBlack x 6
LED_D3.0mm_Horizontal_O1.27mm_Z2.0mm_Clear x 6
PinSocket_1x06_P254mm_Vertical x 2
C_0805_2012Metric x 2
SOT_23 x 5
R_0805_2012Metric x 10
SC0915
SOT_223
MMv3_PCB

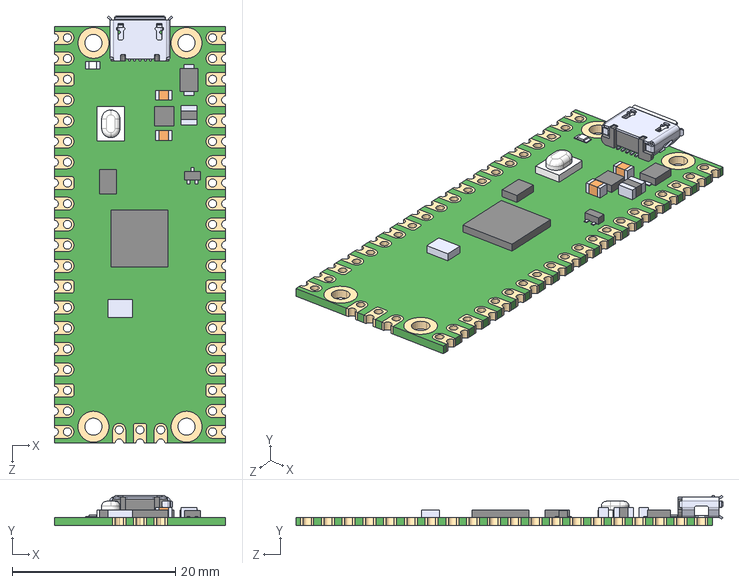
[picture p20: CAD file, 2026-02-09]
board/snapeda/RASPBERRY PI PICO--3DModel-STEP-269445.STEP
21.0 x 3.73 x 52.3 mm

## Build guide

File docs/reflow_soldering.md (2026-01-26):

# Guide: Reflow Soldering Ovens

## Before You Start

* **Inspect PCB:** Components placed correctly, no loose parts.
* **Ensure ventilation is on:** Open the window in SuperNode and turn on the soldering fume extractor
* **Important Note:** The fuse on the reflow oven can melt if the oven is used too many times in a row. Please space out usage and give it time to rest.

## Setting Up the Reflow Oven

### 1. Place the Temperature Probe

<p align="center">
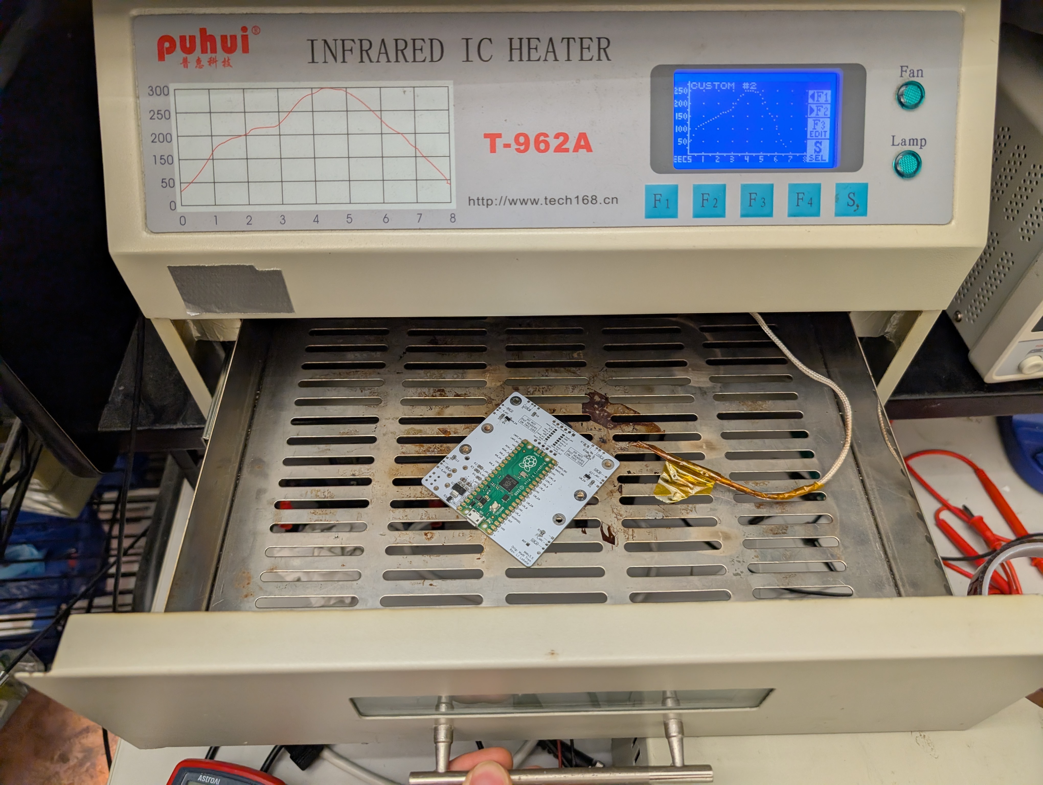
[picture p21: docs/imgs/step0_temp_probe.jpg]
    
    <br>
    <a><b>Place in Oven</b></a>
</p>

The termperature probe is at the end of the white wire. Make sure the probe is not touching heating elements or walls. Ideally, position it near the PCB so it accurately reflects board temperature. Up to two PCBs can be placed in the oven at once.

---

### 2. Power On and Reach the Main Menu

<p align="center">
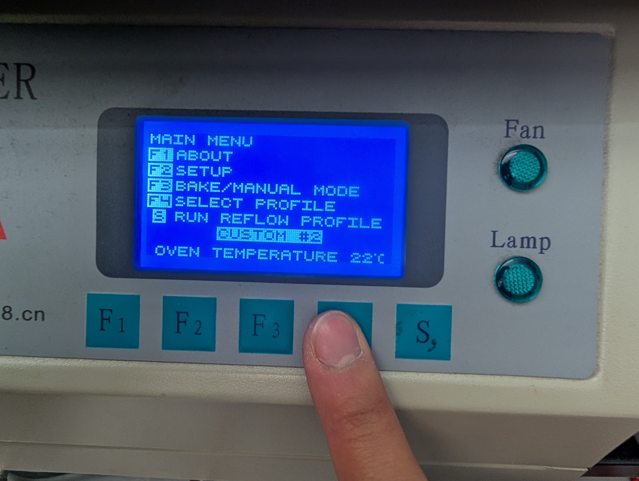
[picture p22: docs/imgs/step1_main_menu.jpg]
    
    <br>
    <a><b>Main Menu</b></a>
</p>

Turn on the oven using the switch in the back and wait for it to boot. You should see the Main Menu screen. Choose F4 to select the profile.

---

### 3. Select the Correct Custom Profile Menu

<p align="center">
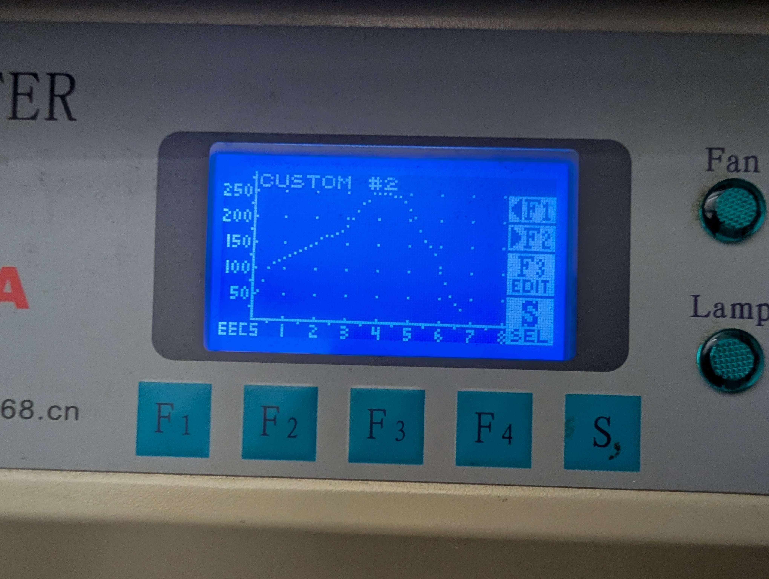
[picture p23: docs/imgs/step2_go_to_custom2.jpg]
    
    <br>
    <a><b>Choose Custom 2</b></a>
</p>
Custom profiles are used for the correct reflow curves. Use F1 and F2 to scroll between the different profiles until you reach CUSTOM #2. Its curve should look similar to the curve printed on the oven to the left. The peak temperature is approximately 250 degrees.

<br>

<p align="center">
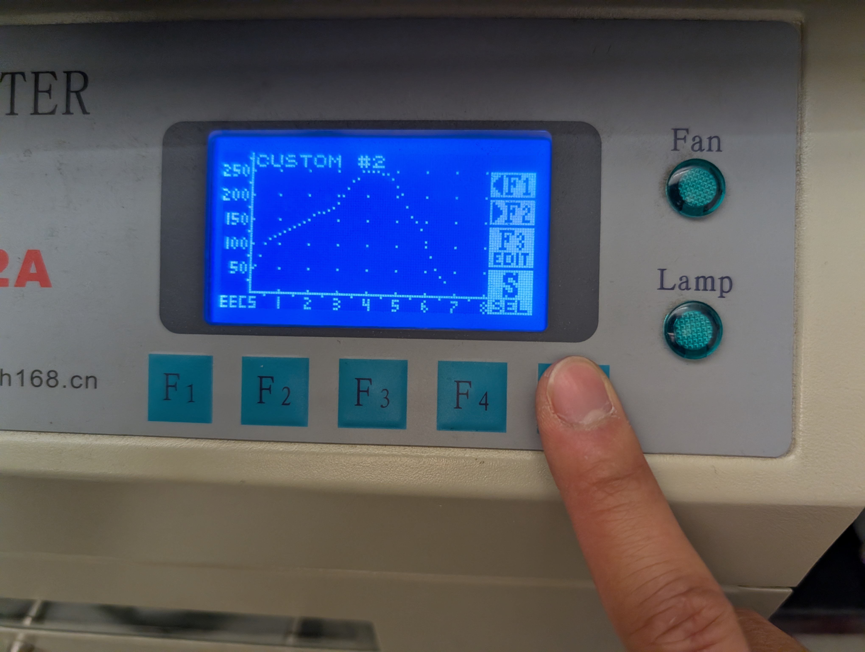
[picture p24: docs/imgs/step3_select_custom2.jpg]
    
    <br>
    <a><b>Select</b></a>
</p>
Click S to select this profile when done.

<br>

---

### 4. Start the Reflow Cycle

<p align="center">
    
    <br>
    <a><b>Click Run</b></a>
</p>
<p align="center">
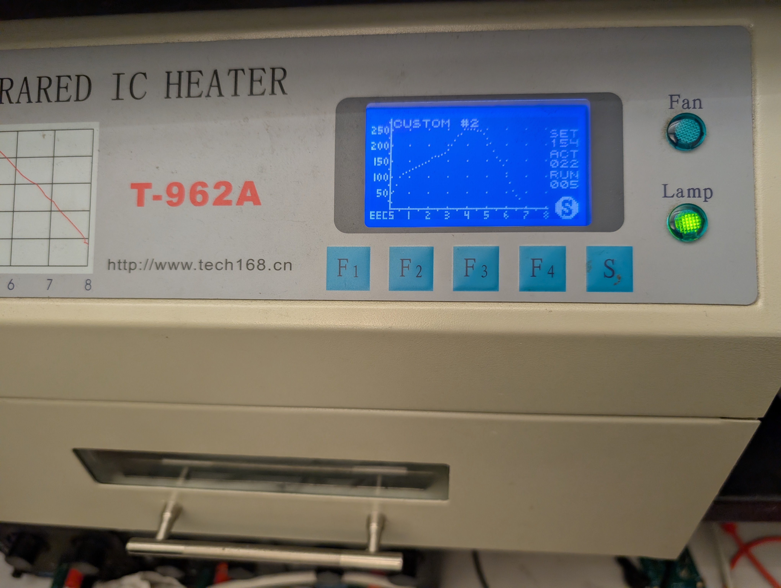
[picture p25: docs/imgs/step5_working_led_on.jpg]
    
    <br>
    <a><b>Oven is on</b></a>
</p>

Press S again to begin the reflow process. The LED indicator should be turned on as shown in the second photo. The oven will automatically progress through the temperatures and is progress will be shown on screen. 

## After the Reflow Cycle

Wait until the oven indicates the cycle is complete and allow some time for it to cool. Carefully remove the board using tweezers or gloves. 

Inspect solder joints for proper connections and no bridging. 
If there are one or two incorrectly done joints or a component has fallen off, they can be hand soldered after.

---

**You’re done!** Once you’ve completed these steps, your PCB should be properly reflow soldered and ready for the rest of assembly.

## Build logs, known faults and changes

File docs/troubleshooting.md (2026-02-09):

# Troubleshooting and Commonly Asked Questions

This document has troubleshooting steps you can take if you are having issues with you mouse in general. Uploading code, MAC vs Windows, and commonly asked questions as well.

MacOS specific problems
1. If your device cannot detect the ____
    - try replugging the cable. If that doesn't work try a different usb-c port. If that doesn't work try another cable from a friend near you ;)
2. You can ____ You cannot upload code to the mouse
    -  Make sure you downloaded the right file
3. You have issues with the screen
    - Try again but better this time jk
    - Try using putty instead... : steps

Lowkey forgot all the other things

---------------------------------------------------------

1. Plug mouse into your computer and upload the latest **firmware.uf2** (see [releases](https://adafruit-circuit-python.s3.amazonaws.com/bin/raspberry_pi_pico/en_US/adafruit-circuitpython-raspberry_pi_pico-en_US-8.2.0.uf2) by dragging the file into the `RPI-RP2` folder that shows up. It should disappear and reappear as a `CIRCUITPY` folder.
    * If you've uploaded firmware before, you'll need to hold the `BOOTSEL` button on the Pi Pico while plugging in.
2. Download the CircuitPython [libraries](https://circuitpython.org/libraries) (Bundle for Version 8.x or 7.x, 9.x is untested! If you'd like you could test it for us ;) ), right click on 8.x -> open in new tab, unzip the file and upload the following folders and files to the lib/ folder on your mouse.
    * adafruit_motor/
    * adafruit_onewire/
    * neopixel.mpy
3. Upload the contents of [sanity/](../labs/sanity/) to the CircuitPython drive that shows up when you plug your mouse into your computer.
4. Find the associated serial port for your mouse.
    <details>
    <summary>Windows</summary>

    Open up `Device Manager` and check the `Ports (COM & LPT)` dropdown. Your serial (COM) port is one of those. If it's hard to identify, try unplugging and replugging your mouse and see which COM port disappears.

    </details>
    <details>
    <summary>MacOS</summary>

    Run `ls  /dev/tty.*` in Terminal. The correct port is one of those. If it's hard to identify, try unplugging and replugging your mouse and see which port disappears.

    </details>
    <details>
    <summary>Linux</summary>

    Hello there! A fellow power user you are. Your distro may be different, but chances are it's under something like `/dev/ttyACM0`.

    </details>
5. Bring up a serial monitor on that serial port (baud rate doesn't matter). There are many options of software to use, but the following are what I personally use.
    * **Windows** - [PuTTY](https://www.chiark.greenend.org.uk/~sgtatham/putty/latest.html) Open up putty -> Serial -> Enter COM[X] -> Run
    * **MacOS** - [SerialTools](https://apps.apple.com/us/app/serialtools/id611021963?mt=12) or [screen](https://en.wikipedia.org/wiki/GNU_Screen) after running ls /dev/tty.* youre going to type into your terminal -> screen "whatever you identified as the correct port". If this doesn't work, its a bit finiky, open up serialTools to the terminal tab change your serial port to the usb you identified and press the connect button on the right hand side. After, press disconnect and do the terminal instructions again.
    * **Linux** - [screen](https://en.wikipedia.org/wiki/GNU_Screen)
6. Follow the instructions printed to the serial monitor. You may have to press CTRL-C and CTRL-D to reset if you don't see anything.
    * IR sensor readings should be around 30,000-60,000 without a surface in front of them and under 5,000 with your hand right in front of them. Speak to a staff member if you need help with this part of the lab!
    * Spin the wheels manually, Encoders should be \~217 ticks per revolution, use the divot in the wheel as a guide :).

> [!IMPORTANT]  
> #### Testing Checkpoint #1 (COMPLETE THIS FIRST! Before moving on)
> - [ ] Connect your micromouse's pi pico to your computer and check that ______
> - [ ] Using the multimeter in lab probe these pads ______
> - [ ] Ensure that connections are made everywhere!

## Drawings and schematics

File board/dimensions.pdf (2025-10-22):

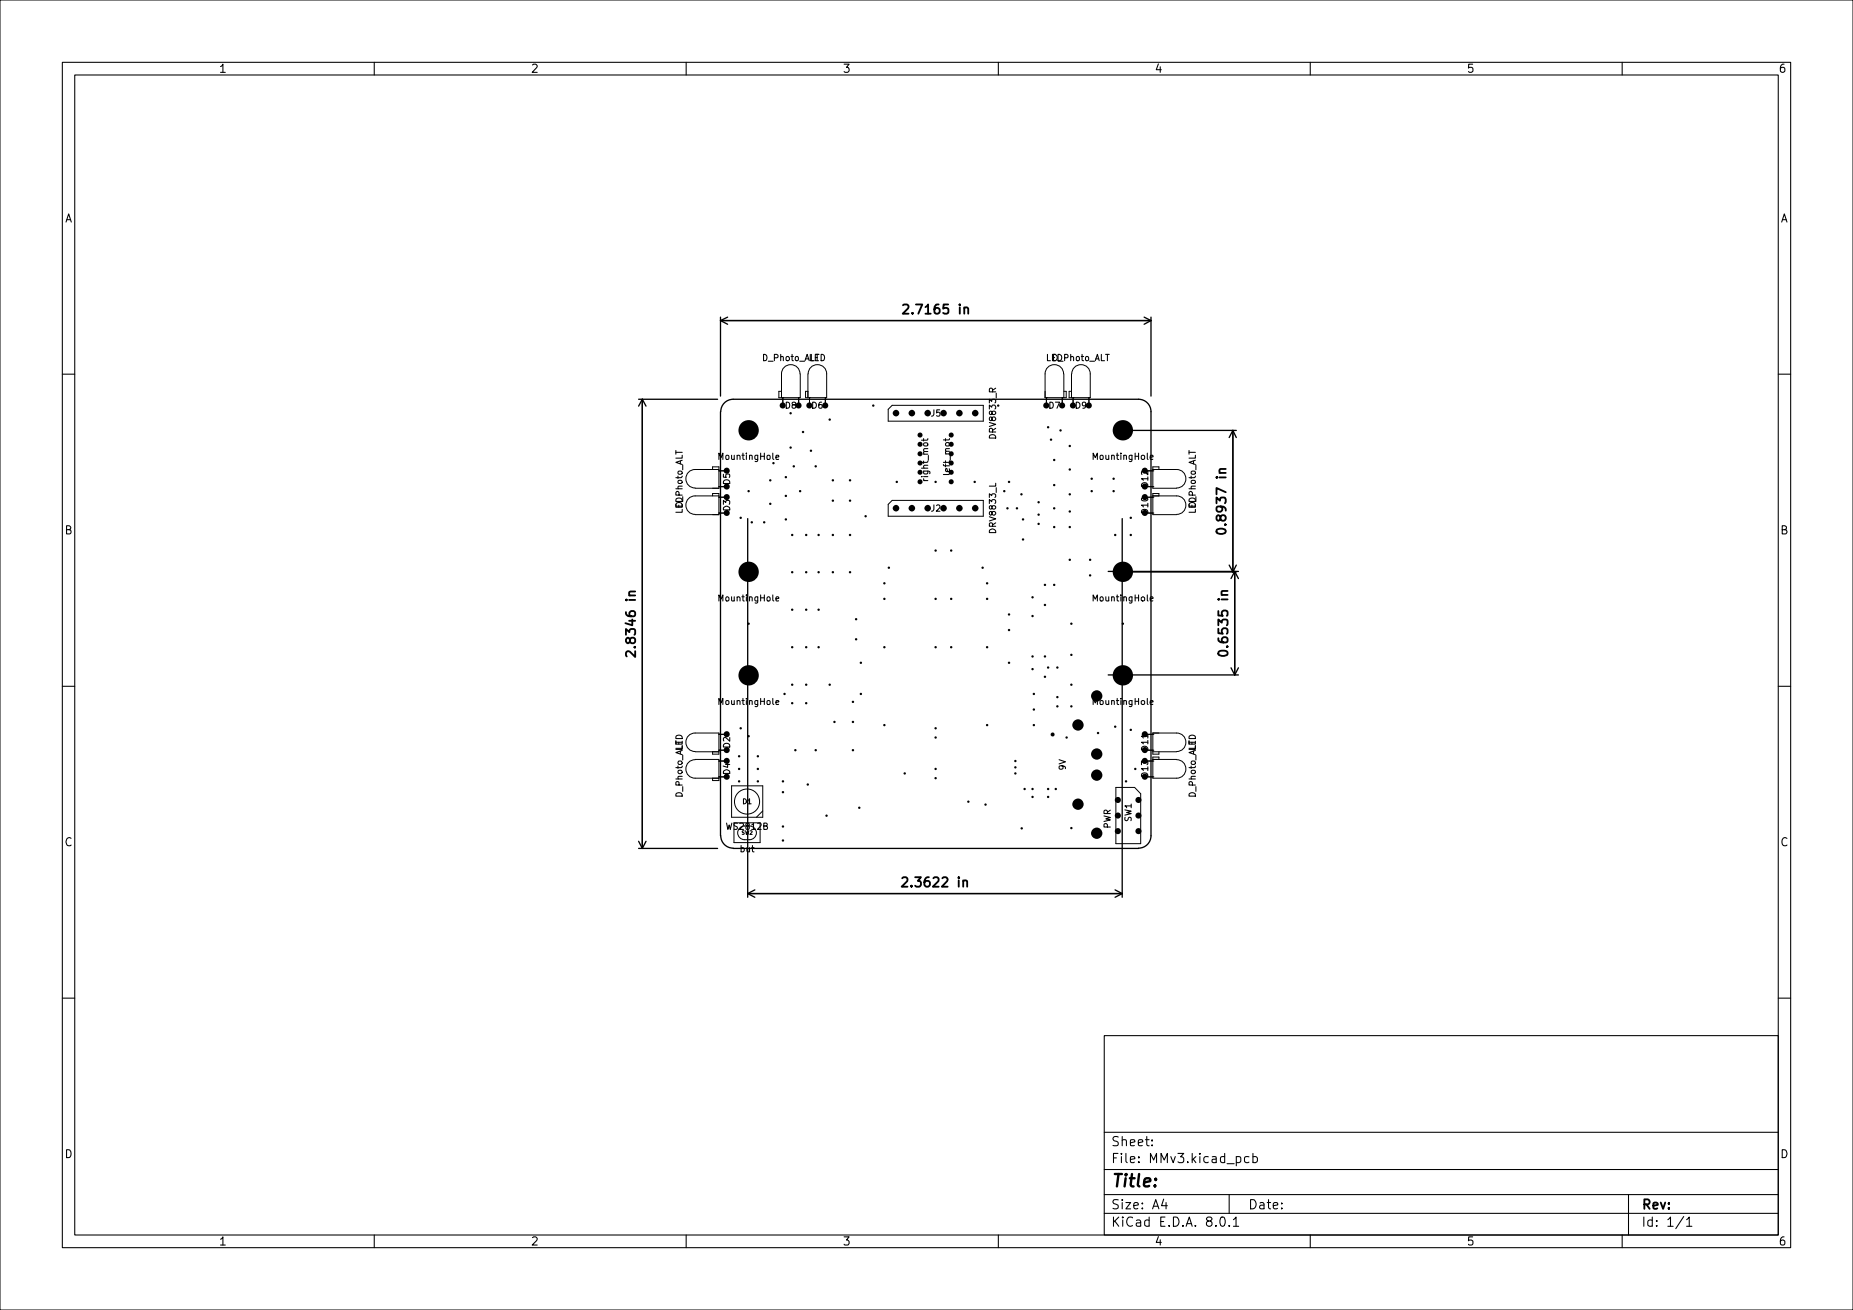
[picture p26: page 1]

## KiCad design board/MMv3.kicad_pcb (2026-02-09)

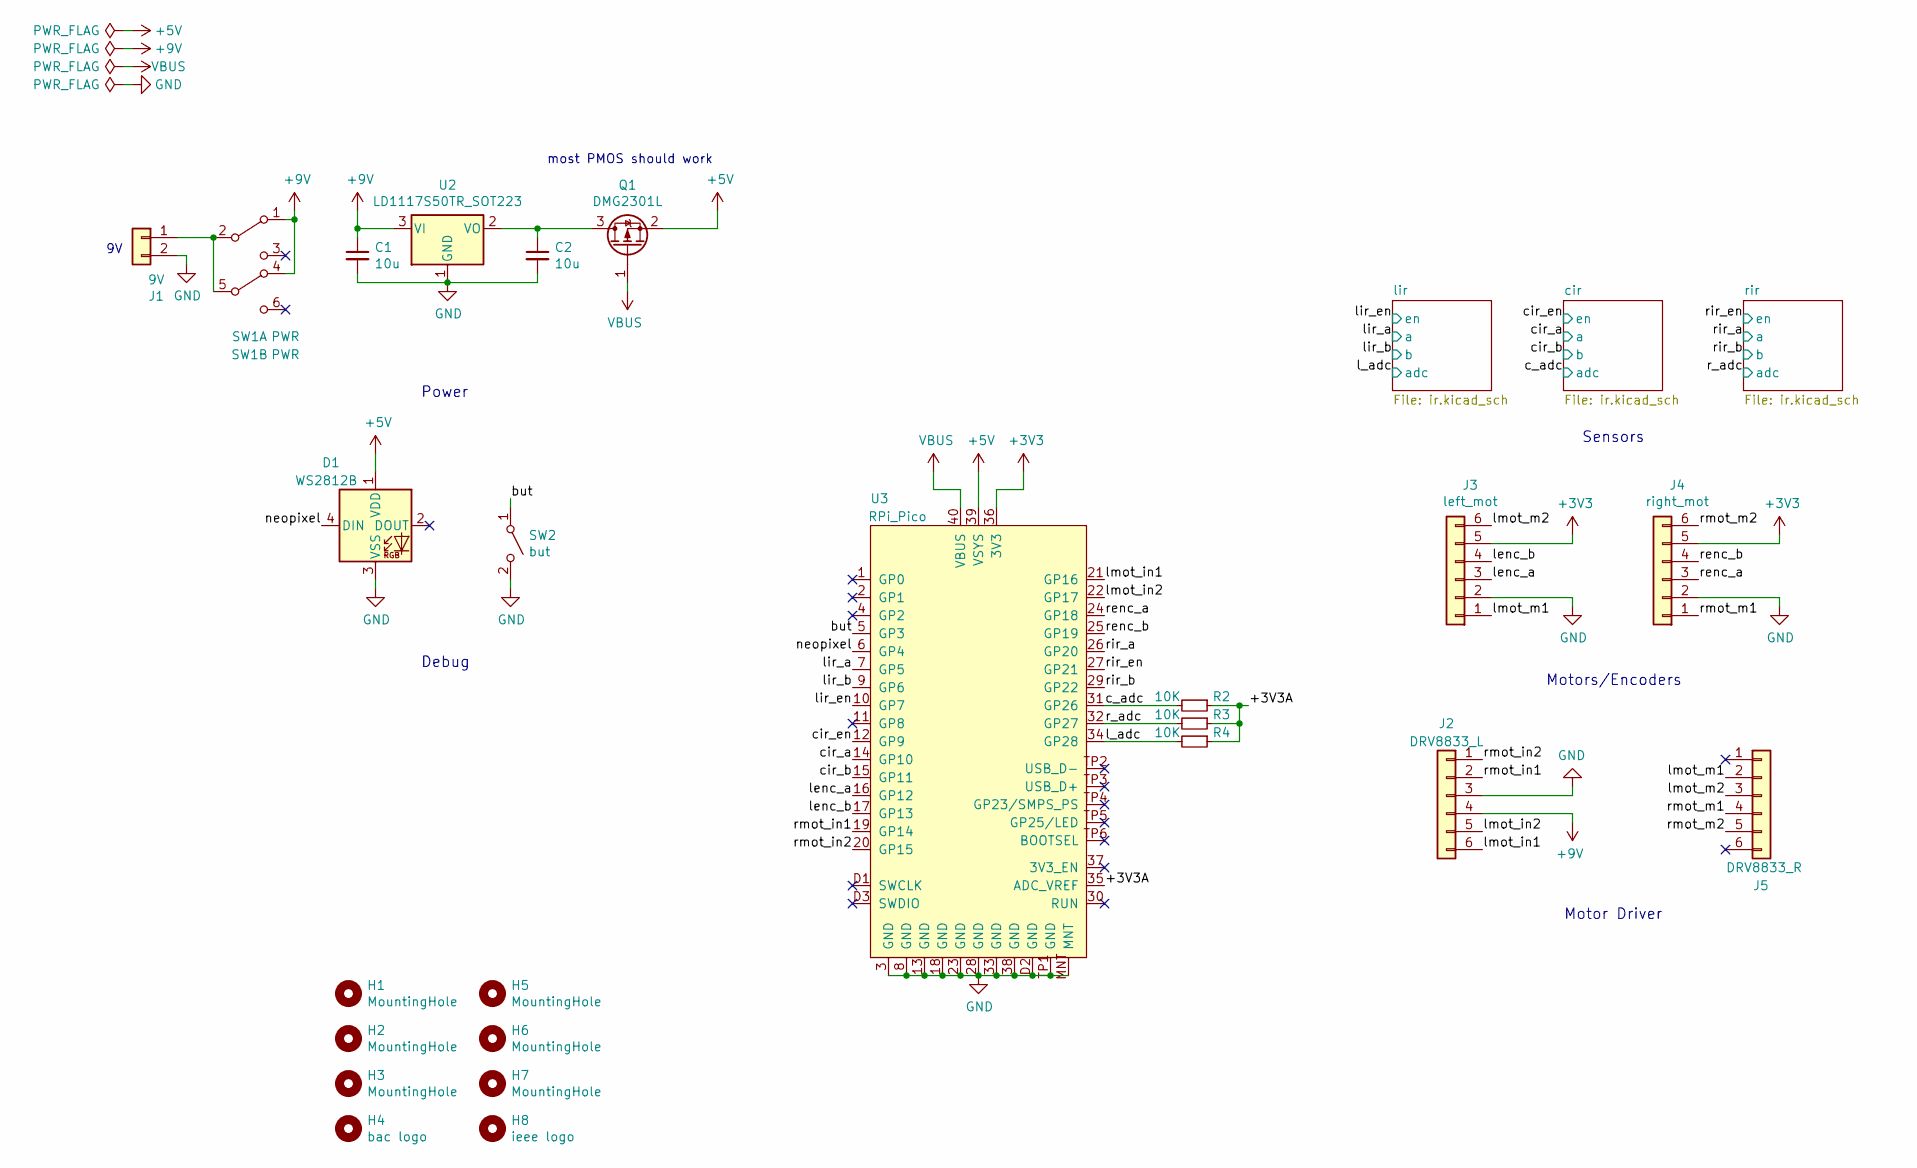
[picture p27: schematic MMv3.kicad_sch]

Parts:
C1, C2: 10u; C_0805_2012Metric
D1: WS2812B; LED_WS2812B_PLCC4_5.0x5.0mm_P3.2mm
H1, H2, H3, H5, H6, H7: MountingHole; MountingHole_3.2mm_M3_Pad_TopBottom
H4: bac logo; bac_logo
H8: ieee logo; ieee_logo
J1: 9V; Keystone_593_594
J2: DRV8833_L; PinSocket_1x06_P2.54mm_Vertical
J3: left_mot; JST_ZH_Vert_6pin
J4: right_mot; JST_ZH_Vert_6pin
J5: DRV8833_R; PinSocket_1x06_P2.54mm_Vertical
Q1: DMG2301L; SOT-23
R2, R3, R4: 10K; R_0805_2012Metric
SW1: PWR; SW_CuK_JS202011CQN_DPDT_Straight
SW2: but; SWDIP2_256X170P100
U2: LD1117S50TR_SOT223; SOT-223-3_TabPin2
U3: RPi_Pico; RPi_Pico_SMD

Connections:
+3V3: J3.5, J4.5, U3.36 (3V3)
+5V: D1.1 (VDD), Q1.2 (S), U3.39 (VSYS); also elsewhere on the board
+9V: C1.1, J2.4, SW1.1 (A), SW1.4 (A), U2.3 (VI)
/+3V3A: R2.1, R3.1, R4.1, U3.35 (ADC_VREF)
/but: SW2.1 (A), U3.5 (GP3)
/c_adc: R2.2, U3.31 (GP26); also elsewhere on the board
/cir_a: U3.14 (GP10); also elsewhere on the board
/cir_b: U3.15 (GP11); also elsewhere on the board
/cir_en: U3.12 (GP9); also elsewhere on the board
/l_adc: R4.2, U3.34 (GP28); also elsewhere on the board
/lenc_a: J3.3, U3.16 (GP12)
/lenc_b: J3.4, U3.17 (GP13)
/lir_a: U3.7 (GP5); also elsewhere on the board
/lir_b: U3.9 (GP6); also elsewhere on the board
/lir_en: U3.10 (GP7); also elsewhere on the board
/lmot_in1: J2.6, U3.21 (GP16)
/lmot_in2: J2.5, U3.22 (GP17)
/lmot_m1: J3.1, J5.2
/lmot_m2: J3.6, J5.3
/neopixel: D1.4 (DIN), U3.6 (GP4)
/r_adc: R3.2, U3.32 (GP27); also elsewhere on the board
/renc_a: J4.3, U3.24 (GP18)
/renc_b: J4.4, U3.25 (GP19)
/rir_a: U3.26 (GP20); also elsewhere on the board
/rir_b: U3.29 (GP22); also elsewhere on the board
/rir_en: U3.27 (GP21); also elsewhere on the board
/rmot_in1: J2.2, U3.19 (GP14)
/rmot_in2: J2.1, U3.20 (GP15)
/rmot_m1: J4.1, J5.4
/rmot_m2: J4.6, J5.5
GND: C1.2, C2.2, D1.3 (VSS), J1.2, J2.3, J3.2, J4.2, SW2.2 (B), U2.1 (GND), U3.3 (GND), U3.8 (GND), U3.13 (GND), U3.18 (GND), U3.23 (GND), U3.28 (GND), U3.33 (GND), U3.38 (GND), U3.D2 (GND), U3.MNT, U3.TP1 (GND); also elsewhere on the board
unnamed: J1.1, SW1.2 (B), SW1.5 (B)
unnamed: C2.1, Q1.3 (D), U2.2 (VO)
VBUS: Q1.1 (G), U3.40 (VBUS)

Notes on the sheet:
Motor Driver
Sensors
Power
Motors/Encoders
most PMOS should work
Debug

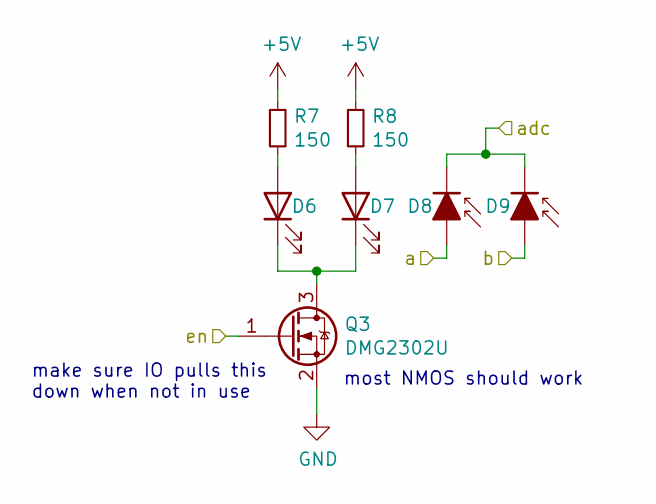
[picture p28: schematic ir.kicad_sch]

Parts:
D6, D7: LED; LED_D3.0mm_RH_THT_Clear
D8, D9: D_Photo_ALT; LED_D3.0mm_RH_THT_IRBlack
Q3: DMG2302U; SOT-23
R7, R8: 150; R_0805_2012Metric

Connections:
+5V: R7.1, R8.1; also elsewhere on the board
/c_adc: D8.1 (K), D9.1 (K); also elsewhere on the board
/cir_a: D8.2 (A); also elsewhere on the board
/cir_b: D9.2 (A); also elsewhere on the board
/cir_en: Q3.1 (G); also elsewhere on the board
GND: Q3.2 (S); also elsewhere on the board
unnamed: D6.2 (A), R7.2
unnamed: D6.1 (K), D7.1 (K), Q3.3 (D)
unnamed: D7.2 (A), R8.2

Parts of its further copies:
D2, D3, D10, D11: LED; LED_D3.0mm_RH_THT_Clear
D4, D5, D12, D13: D_Photo_ALT; LED_D3.0mm_RH_THT_IRBlack
Q2, Q4: DMG2302U; SOT-23
R5, R6, R9, R10: 150; R_0805_2012Metric

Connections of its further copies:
+5V: R5.1, R6.1, R9.1, R10.1; also elsewhere on the board
/l_adc: D4.1 (K), D5.1 (K); also elsewhere on the board
/lir_a: D4.2 (A); also elsewhere on the board
/lir_b: D5.2 (A); also elsewhere on the board
/lir_en: Q2.1 (G); also elsewhere on the board
/r_adc: D12.1 (K), D13.1 (K); also elsewhere on the board
/rir_a: D12.2 (A); also elsewhere on the board
/rir_b: D13.2 (A); also elsewhere on the board
/rir_en: Q4.1 (G); also elsewhere on the board
GND: Q2.2 (S), Q4.2 (S); also elsewhere on the board
unnamed: D2.2 (A), R5.2
unnamed: D2.1 (K), D3.1 (K), Q2.3 (D)
unnamed: D3.2 (A), R6.2
unnamed: D10.2 (A), R9.2
unnamed: D10.1 (K), D11.1 (K), Q4.3 (D)
unnamed: D11.2 (A), R10.2

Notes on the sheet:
make sure IO pulls this down when not in use
most NMOS should work

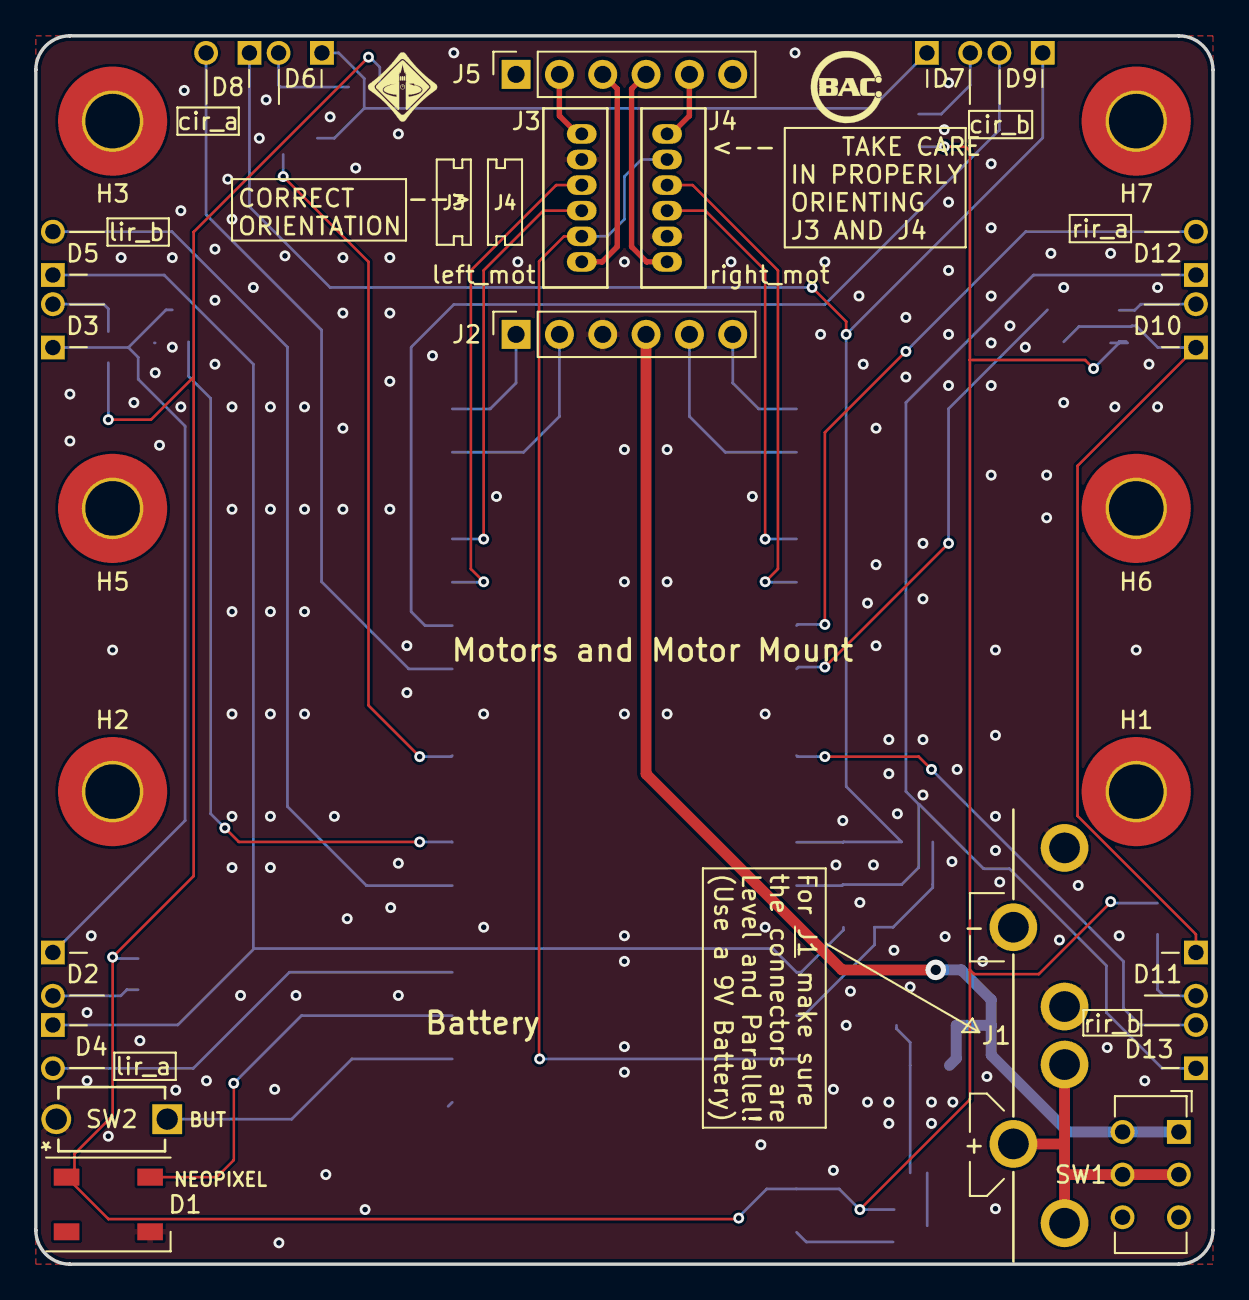
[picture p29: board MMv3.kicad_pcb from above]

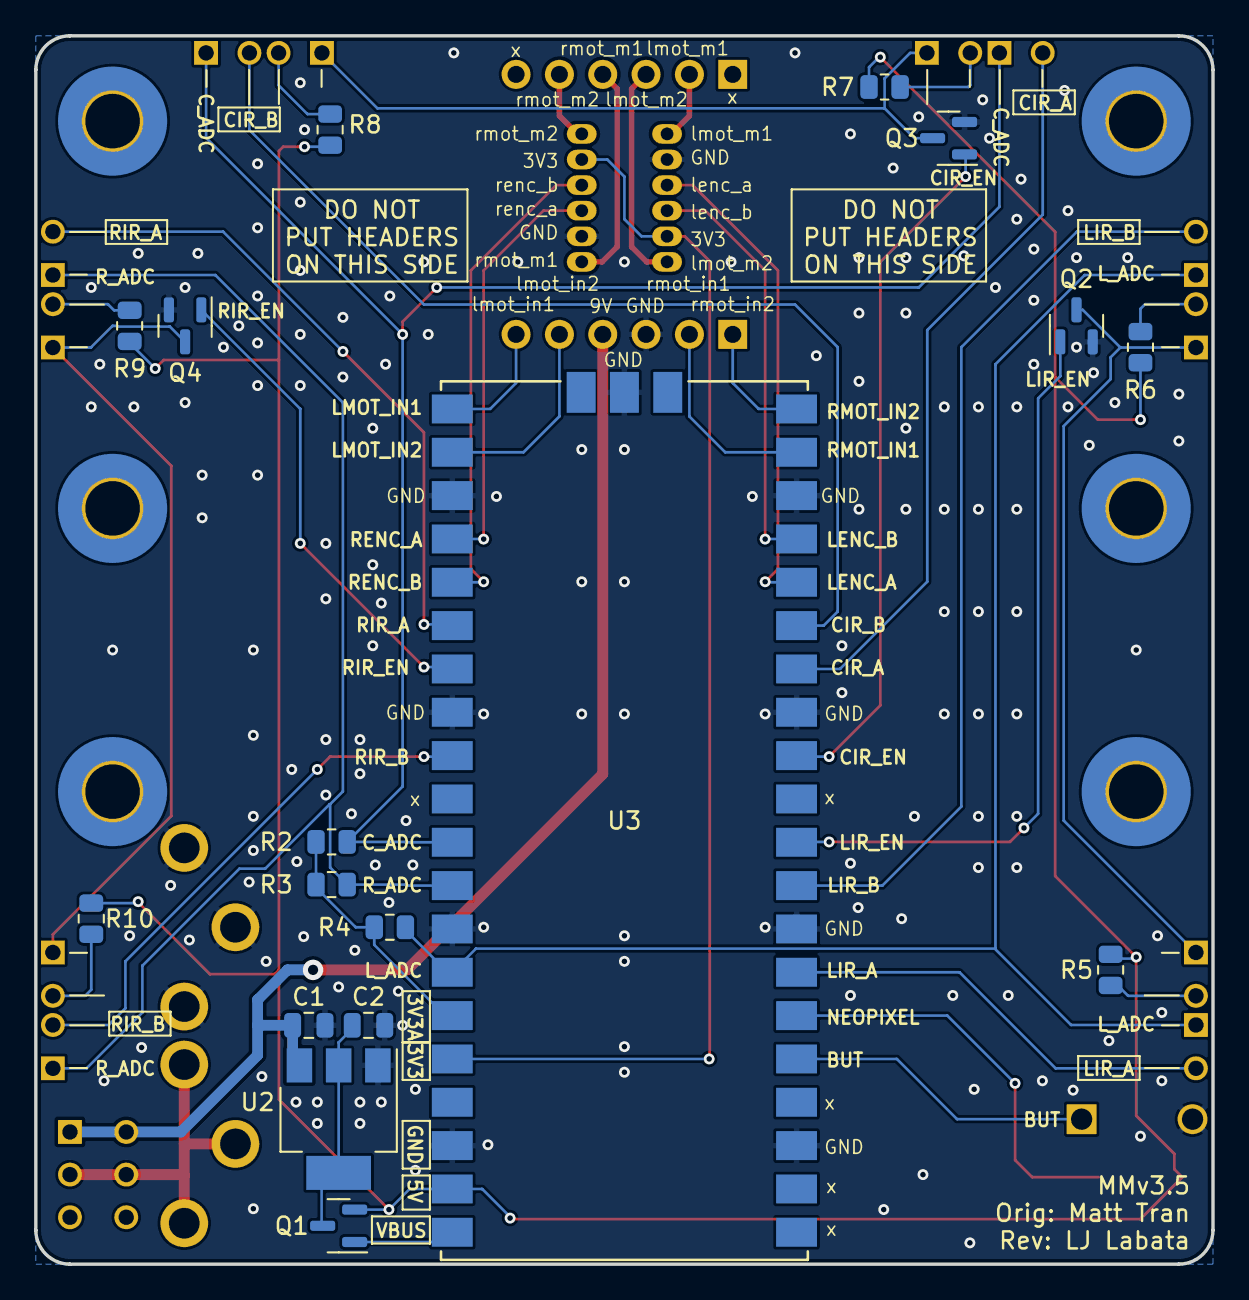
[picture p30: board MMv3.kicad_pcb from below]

Board: 2 copper layers, 69.0 x 72.0 mm, 45 parts (17 on the bottom side), 43 nets.

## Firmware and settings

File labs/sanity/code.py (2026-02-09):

import board
import time

import digitalio
import neopixel
import rotaryio
import pwmio

# from ds28e05  import DS28E05
from irsensor import IRSensors
import adafruit_motor.motor as motor

""" Peripherals """

# debug
led = digitalio.DigitalInOut(board.LED)
led.direction = digitalio.Direction.OUTPUT

but = digitalio.DigitalInOut(board.GP3)
but.pull = digitalio.Pull.UP

rgb = neopixel.NeoPixel(board.GP4, 1)

# extra stuffs
# eeprom = DS28E05(board.GP2)

# IR sensors
ir = IRSensors(
    board.GP7,  board.GP5,  board.GP6,  board.GP28, # left
    board.GP9,  board.GP10, board.GP11, board.GP26, # center
    board.GP21, board.GP20, board.GP22, board.GP27  # right
)

# encoders
lenc = rotaryio.IncrementalEncoder(board.GP12, board.GP13)
renc = rotaryio.IncrementalEncoder(board.GP19, board.GP18)

# motors
lmot = motor.DCMotor(
    pwmio.PWMOut(board.GP16, frequency=20000),
    pwmio.PWMOut(board.GP17, frequency=20000)
)
rmot = motor.DCMotor(
    pwmio.PWMOut(board.GP15, frequency=20000),
    pwmio.PWMOut(board.GP14, frequency=20000)
)
lmot.decay_mode = motor.SLOW_DECAY
rmot.decay_mode = motor.SLOW_DECAY

""" Main """

if __name__ == "__main__":
    # debug
    print("Hello World! Press the button next to the battery to begin tests.")
    while (but.value):
        pass

    print("Blinking the LED underneath your micromouse...")
    for _ in range(6):
        led.value = not led.value
        time.sleep(0.25)

    print("Turning on Neopixel on top of your micromouse...")
    rgb[0] = (255, 0, 0)
    time.sleep(0.5)
    rgb[0] = (0, 255, 0)
    time.sleep(0.5)
    rgb[0] = (0, 0, 255)
    time.sleep(0.5)
    rgb[0] = (1, 1, 1)

    # extra stuffs
    # if eeprom.devices:
    #     print("Detected the following 1-Wire devices...")
    #     for d in eeprom.devices:
    #         print("\t", "".join("{:02x}".format(x) for x in d.rom))

    #     eeprom.write(0, 0, b'MMv3.1')
    #     if not eeprom.read(0, 0, 6) == b'MMv3.1':
    #         print("FAIL! EEPROM write mismatch!")
    # else:
    #     print("FAIL! No 1-Wire devices detected!")

    # IR sensors
    print("Scanning IR sensors! Press button next to the battery to start and stop.")
    while (but.value):
        pass
    time.sleep(0.05)
    while (not but.value):
        pass

    while (but.value):
        ir.scan()
        print("lir_a:", ir.lir_a, "\t", "lir_b:", ir.lir_b, "\t",
                "cir_a:", ir.cir_a, "\t", "cir_b:", ir.cir_b, "\t",
                "rir_a:", ir.rir_a, "\t", "rir_b:", ir.rir_b
        )
        time.sleep(0.05)
    time.sleep(0.05)
    while (not but.value):
        pass

    # encoders
    print("Reading encoders! Press button next to the battery to start and stop.")
    while (but.value):
        pass
    time.sleep(0.05)
    while (not but.value):
        pass

    while (but.value):
        print("lenc:", lenc.position, "\t", "renc:", renc.position)
        time.sleep(0.05)
    time.sleep(0.05)
    while (not but.value):
        pass

    # motors
    print("Testing motors! Plug in battery and turn on switch. Press button next to the battery to start.")
    print("(Beware your mouse may begin to run off on its own. You may want to pick it up just in case ;))\n")

    while (but.value):
        pass

    print("Did you actually turn on the switch? You can tell if the red LED light underneath the motor driver is on. If so, please press the button next to the battery to actually make the test the motors please.\n")

    time.sleep(0.5)
    
    while (but.value):
        pass

    print("Full speed forward")
    lmot.throttle = 1
    rmot.throttle = 1
    time.sleep(0.5)
    print("Brake")
    lmot.throttle = 0
    rmot.throttle = 0
    time.sleep(0.5)
    print("Full speed backward")
    lmot.throttle = -1
    rmot.throttle = -1
    time.sleep(0.5)
    print("Brake")
    lmot.throttle = 0
    rmot.throttle = 0
    time.sleep(0.5)
    print("Low speed forward")
    lmot.throttle = 0.25
    rmot.throttle = 0.25
    time.sleep(0.5)
    print("Brake")
    lmot.throttle = 0
    rmot.throttle = 0
    time.sleep(0.5)
    print("Low speed backward")
    lmot.throttle = -0.25
    rmot.throttle = -0.25
    time.sleep(0.5)
    print("Brake")
    lmot.throttle = 0
    rmot.throttle = 0
    time.sleep(0.5)

    print("Done with tests!\n")
    
    print("Press button next to the battery to just drive straight now :P")
    print("Forever! :O\n")

    while (but.value):
        pass

    print("JK!\n")
    time.sleep(1)
    print("IMPORTANT (please read the following as it will make using your mouse easier):")
    print(" 1) Hit 'Ctrl + C', while in the screen/serial monitor/etc or flip the switch off to stop the mouse.")
    print(" 2) If you have hit 'Ctrl + C' but now want your program to run again hit 'Ctrl  + D' now in order to reload your program. This is assuming you haven't made any changes to your code and you already uploaded your program into your Pi Pico after having hit 'Ctrl + C' \n")


    print("Please press the button next to the battery now to actually make the mouse drive straight\n")
    
    while (but.value):
        pass

    while True:
        delta = lenc.position - renc.position
        u = 0.001 * delta
        lmot.throttle = 0.25 - u
        rmot.throttle = 0.25 + u
        print(delta)
        time.sleep(0.05)

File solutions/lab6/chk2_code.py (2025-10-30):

import board
import time
from math import pi

import digitalio
import neopixel
import rotaryio
import pwmio
import adafruit_motor.motor as motor

""" Constants """

ENCODER_TICKS_PER_REVOLUTION = 145
WHEELBASE_DIAMETER = 78.0 # mm
WHEEL_DIAMETER = 34.0 # mm

""" Peripherals """

but = digitalio.DigitalInOut(board.GP3)
but.pull = digitalio.Pull.UP

# encoders
lenc = rotaryio.IncrementalEncoder(board.GP12, board.GP13)
renc = rotaryio.IncrementalEncoder(board.GP19, board.GP18)

# motors
lmot = motor.DCMotor(
    pwmio.PWMOut(board.GP16, frequency=20000),
    pwmio.PWMOut(board.GP17, frequency=20000)
)
rmot = motor.DCMotor(
    pwmio.PWMOut(board.GP15, frequency=20000),
    pwmio.PWMOut(board.GP14, frequency=20000)
)
lmot.decay_mode = motor.SLOW_DECAY
rmot.decay_mode = motor.SLOW_DECAY

""" Main """

def constrain(val, min_val, max_val):
    return min(max_val, max(val, min_val))

if __name__ == "__main__":
    MM_PER_TICK = pi * WHEEL_DIAMETER / ENCODER_TICKS_PER_REVOLUTION
    while True:
        left_dist  = lenc.position * MM_PER_TICK
        right_dist = renc.position * MM_PER_TICK

        dist  = (left_dist + right_dist) / 2
        theta = (right_dist - left_dist) / WHEELBASE_DIAMETER

        # angular P control
        Kp_ang = 0.3
        theta_target = 0.0

        angular_error = theta_target - theta
        steer_correction = Kp_ang * angular_error

        # linear P control
        Kp_lin = 0.01
        dist_target = 200 # in mm

        # linear error?
        lin_error = dist_target - dist
        lin_correction = constrain(Kp_lin * lin_error, -0.3, 0.3)

        # combine
        lmot.throttle = constrain(lin_correction - steer_correction, -1, 1)
        rmot.throttle = constrain(lin_correction + steer_correction, -1, 1)

        print(angular_error, lin_error)

        time.sleep(0.05)

''' OLD'''
# import board
# import time
# from math import pi

# import digitalio
# import neopixel
# import rotaryio
# import pwmio
# import adafruit_motor.motor as motor

# """ Constants """

# ENCODER_TICKS_PER_REVOLUTION = 217
# WHEELBASE_DIAMETER = 78.0 # mm
# WHEEL_DIAMETER = 34.0 # mm

# """ Peripherals """

# # debug
# led = digitalio.DigitalInOut(board.LED)
# led.direction = digitalio.Direction.OUTPUT

# but = digitalio.DigitalInOut(board.GP3)
# but.pull = digitalio.Pull.UP

# rgb = neopixel.NeoPixel(board.GP4, 1)

# # encoders
# lenc = rotaryio.IncrementalEncoder(board.GP12, board.GP13)
# renc = rotaryio.IncrementalEncoder(board.GP19, board.GP18)

# # motors
# lmot = motor.DCMotor(
#     pwmio.PWMOut(board.GP16, frequency=20000),
#     pwmio.PWMOut(board.GP17, frequency=20000)
# )
# rmot = motor.DCMotor(
#     pwmio.PWMOut(board.GP15, frequency=20000),
#     pwmio.PWMOut(board.GP14, frequency=20000)
# )
# lmot.decay_mode = motor.SLOW_DECAY
# rmot.decay_mode = motor.SLOW_DECAY

# """ Main """

# def constrain(val, min_val, max_val):
#     return min(max_val, max(val, min_val))

# if __name__ == "__main__":
#     MM_PER_TICK = pi * WHEEL_DIAMETER / ENCODER_TICKS_PER_REVOLUTION

#     while True:
#         left_dist  = lenc.position * MM_PER_TICK
#         right_dist = renc.position * MM_PER_TICK

#         dist  = (left_dist + right_dist) / 2
#         theta = (right_dist - left_dist) / WHEELBASE_DIAMETER

#         # angular P control
#         Kp_ang = 0.1
#         theta_target = 0

#         e_ang = theta_target - theta
#         u_ang = Kp_ang * e_ang

#         # linear P control
#         Kp_lin = 0.01
#         dist_target = 200

#         e_lin = dist_target - dist
#         u_lin = constrain(Kp_lin * e_lin, -0.3, 0.3) # 0.9 is a bit too fast

#         # combine
#         lmot.throttle = constrain(u_lin - u_ang, -1, 1)
#         rmot.throttle = constrain(u_lin + u_ang, -1, 1)

#         print(e_ang, e_lin)

#         time.sleep(0.05)

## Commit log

2025-02-22 First Merge of IR and Encoder
    Changed around lab names for IR and Encoder (3->4) and file names overall (when the merge happens we will get rid of the original labs). Adjusted the IR lab to be more informational than menial.
2025-04-23 Create lab PID
2025-04-23 Rename solutions/lab5/checkoff.md to solutions/lab 5(PID)
2025-04-23 Rename solutions/lab 5(PID) to solutions/lab 5.5/checkoff.md
2025-10-22 Added dimensions to pcb and also printed out a pdf of the dimensions
    [MMv3.kicad_pcb]
2025-10-23 Fixed the ordering of when to assemble motors
2025-12-19 Added 3D .step model of Pi Pico and whatever other settings and changes I forgot
    [MMv3.kicad_pcb, MMv3.kicad_sch, RASPBERRY PI PICO--3DModel-STEP-269445.STEP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]
2025-12-24 Finished silkscreen and moving components
    [MMv3.kicad_pcb, MMv3.kicad_sch, MMv3.step]
2025-12-24 Changed silkscreen from 3.4 to 3.5
    [MMv3.kicad_pcb]
2025-12-24 Beginning 9V Battery LED indicator schematic circuit
    [MMv3.kicad_sch]
2025-12-31 first time running through instantDFM
    [MMv3.kicad_pcb, MMv3.kicad_sch, ir.kicad_sch]
2026-01-06 finished mmv3_5 now bought
    [MMv3.kicad_pcb, MMv3.kicad_sch]
2026-01-24 Update CircuitPython library download instructions
2026-01-24 Enhance user prompts for clarity in main execution flow
2026-01-26 Added reflow soldering guide
2026-02-09 finished adding changes and updates to lab2 assembly
